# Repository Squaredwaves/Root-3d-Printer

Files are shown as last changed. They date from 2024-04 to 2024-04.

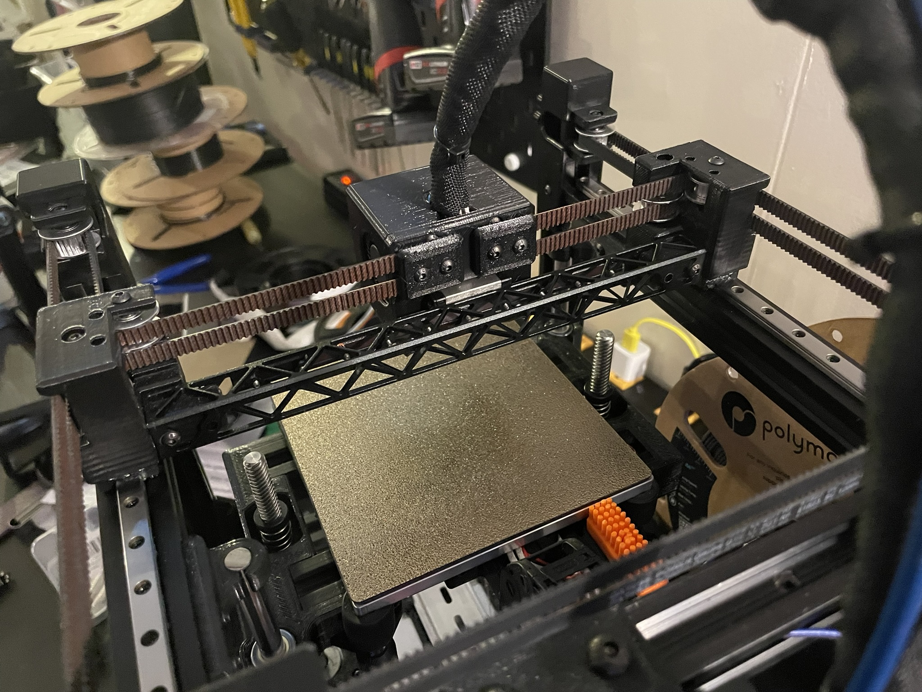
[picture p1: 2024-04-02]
Pics/Print head rear.jpeg

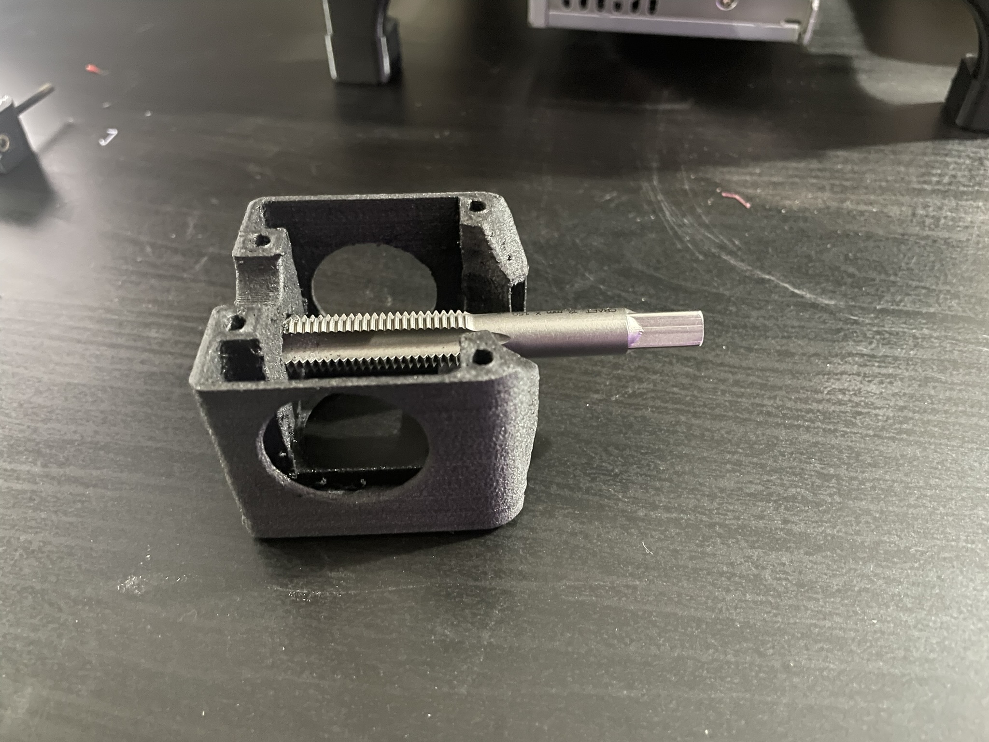
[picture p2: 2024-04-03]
Hot end assembly/IMG_1050.JPEG

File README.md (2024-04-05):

# Root-3d-Printer
Pics, files, and instructions for Root 3d Printer

Printables Link: https://www.printables.com/model/829074/edit

Instructions to come...



************Hot end assembly****************


Clean up any stringing or blobs as best as you can. This was some junk tier cf-petg


Run an m12x1.5 tap through threaded portion to chase threads and remove excess material




Press in m3 heat sets



Install heat break fan. Top first then bottom should clip in with a little pressure in the corners. Align wire so it doesn't get in the way


Prepare parts cooling fans by cliping the little plastic retainer on the fan and pulling the wire (gently) back



I will usually install the right one first but it probobly doesnt matter. They are a tight fit and may not come back out in one piece so make sure its how you want it.


Install Revo Micro hear break. I find a 10mm m4 bolt through the bottom helps a lot


Prep heater by CAREFULLY bending strain relief to a 90ish degree angle


Attach to heat break


Press 4 heat sets into back plate and attach to x axis linear rail
The completed hot end  bolts in from the back with m3 bolts

can see the top two bolts under belt retention

***************MOTOR MOUNTS ASSEMBLY********************




Press heat sets into shown location 


Thread 2 long m3 bolts from the bottomthrough the heatsets


Prep attachment bolts and hammer head nuts


Install in back corner of frame


Install motor with toothed pulley. I used a 2mm allen wrench between the motor body and pulley for spacing



Start installing pulleys. For left mount it will be 2 smooth on the inside and one smooth on the bottom one on the top on the outside(the picture is incorect on toothed pulley location) 2 or 3 3x5 .5mm shims go between the pulleys. Amazon link - https://www.amazon.com/gp/product/B08ZYLHGC9/ref=ppx_yo_dt_b_search_asin_title?ie=UTF8&th=1


Install top hat. Bolts should just poke through the top. 2 3mm bolts on either side hold to main body.


I don't know if its needed but I snugged acouple nuts on top

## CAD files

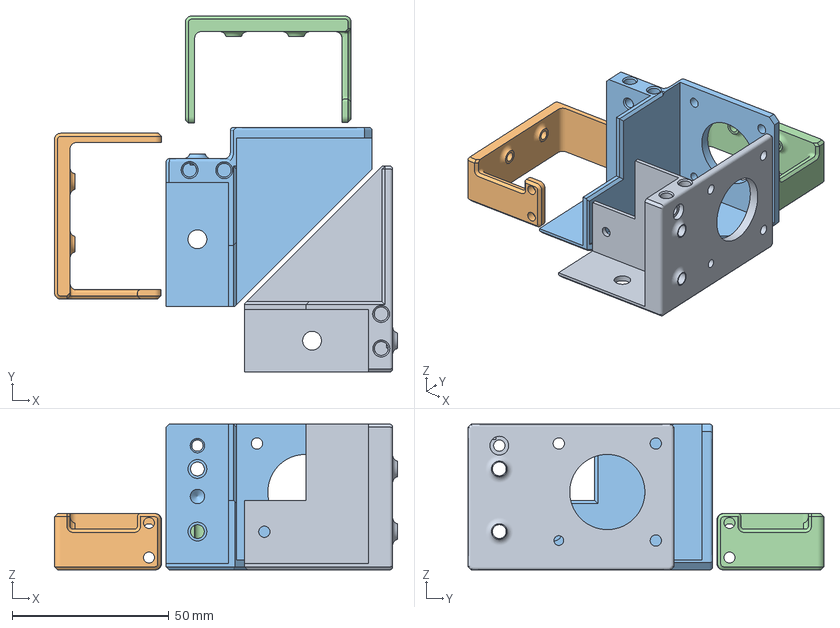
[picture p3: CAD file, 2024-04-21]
ROOT/REAR_CORNERS_MOTOR_MOUNTS.3mf
109.6 x 113.7 x 46.6 mm

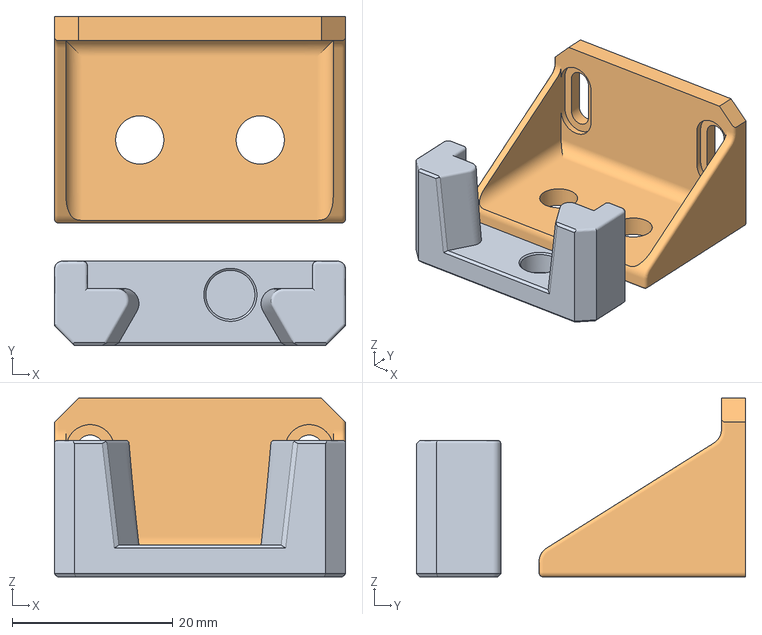
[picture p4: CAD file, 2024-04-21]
ROOT/KLICKYPCB_FRAMEMOUNT.3mf
36.3 x 41.0 x 22.3 mm

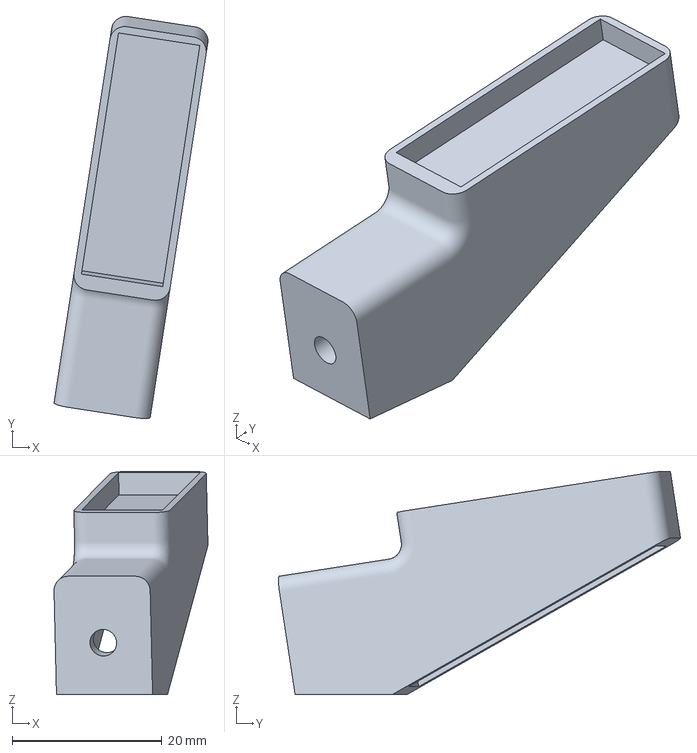
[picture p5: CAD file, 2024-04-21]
ROOT/NOZZLE_BRUSH.3mf
20.6 x 53.7 x 29.8 mm

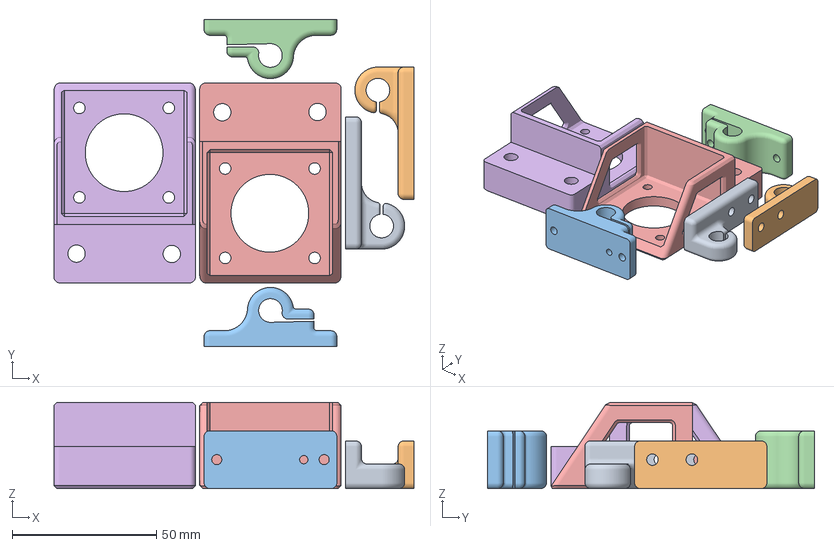
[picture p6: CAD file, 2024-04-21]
ROOT/Z_MOTION_MOTORS.3mf
124.7 x 113.4 x 29.8 mm
bed motor mounts.3mf
bed motor mounts.3mf(1)
bed motor mounts.3mf(2)
bed motor mounts.3mf(3)
bed motor mounts.3mf(4)
bed motor mounts.3mf(5)

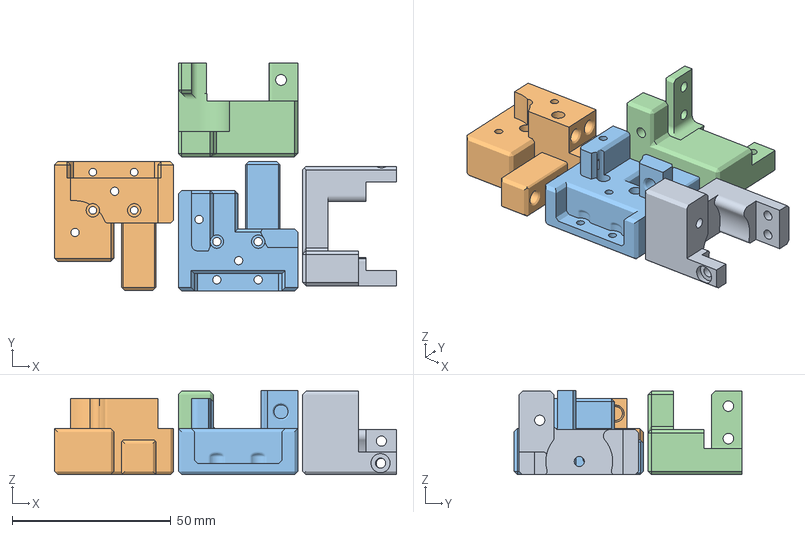
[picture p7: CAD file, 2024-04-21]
ROOT/XY.3mf
107.5 x 71.6 x 26.4 mm

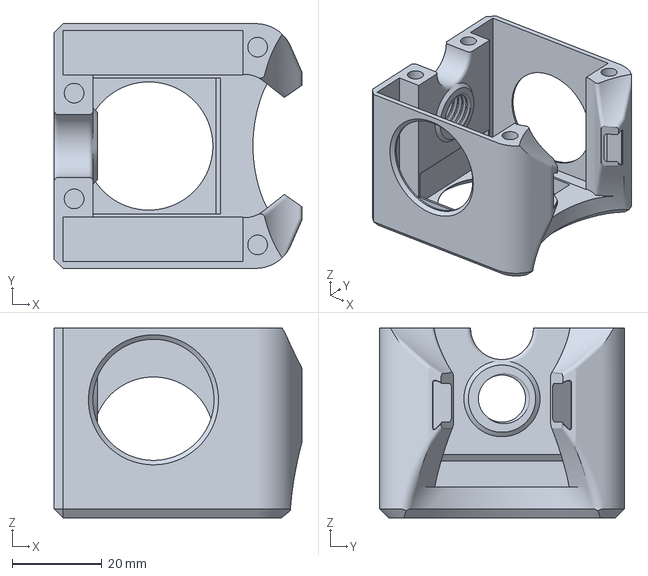
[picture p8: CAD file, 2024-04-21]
ROOT/FAN_SHROUD.3mf
55.3 x 54.6 x 42.3 mm

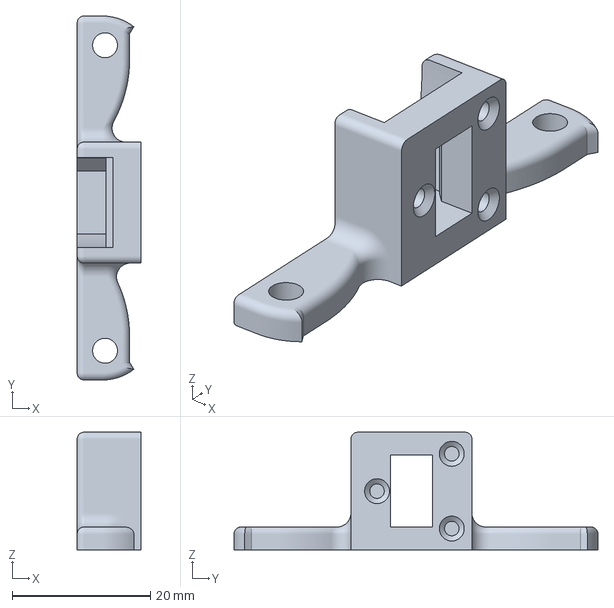
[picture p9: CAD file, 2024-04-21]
ROOT/Klicky_PCb_printmount.3mf
9.20 x 52.6 x 17.0 mm

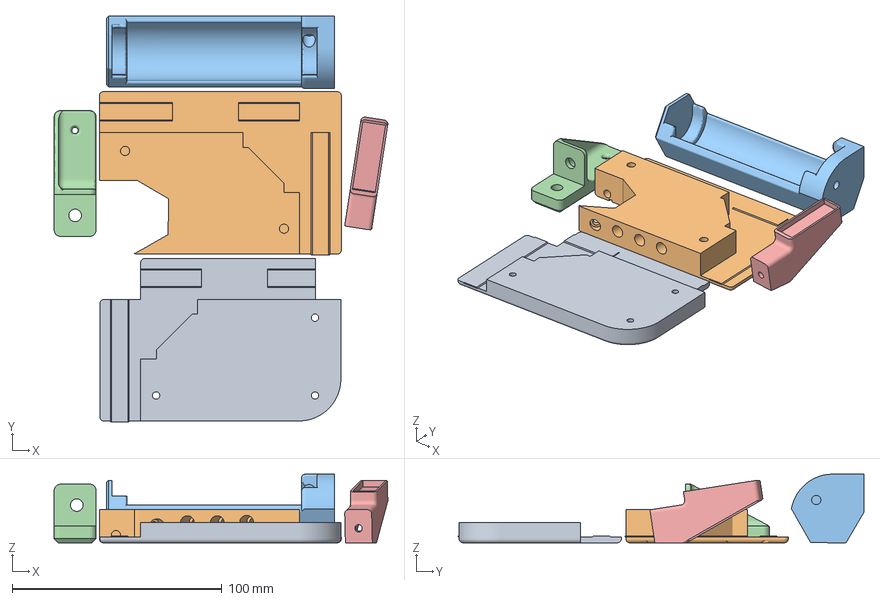
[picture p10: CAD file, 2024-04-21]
ROOT/FILAMENT_MANAGEMENT.3mf
159.1 x 193.6 x 32.8 mm
FILAMENT_MANAGEMENT.3mf(1)
FILAMENT_MANAGEMENT.3mf(2)
FILAMENT_MANAGEMENT.3mf(3)
FILAMENT_MANAGEMENT.3mf(4)
FILAMENT_MANAGEMENT.3mf(5)

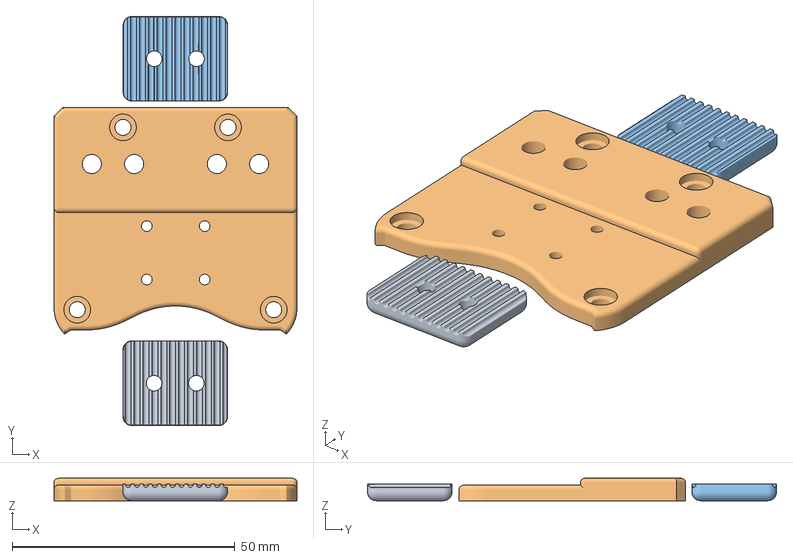
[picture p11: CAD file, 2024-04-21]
ROOT/PRINT_HEAD_TO_RAIL.3mf
54.6 x 91.9 x 5.06 mm
PRINT_HEAD.3mf
PRINT_HEAD.3mf(1)
PRINT_HEAD.3mf(2)

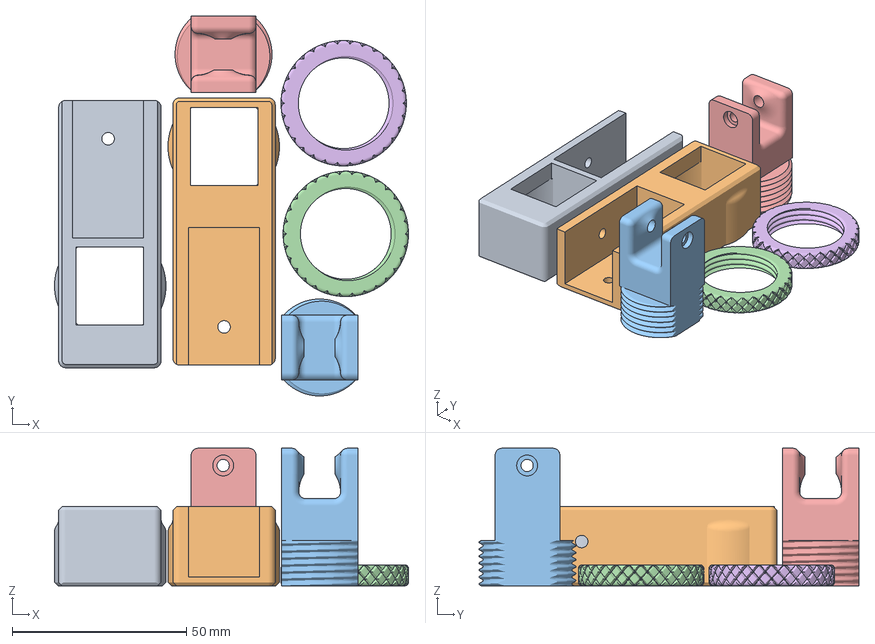
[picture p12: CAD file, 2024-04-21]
ROOT/FRONT_CORNERS_TENSIONERS.3mf
101.6 x 109.1 x 39.5 mm

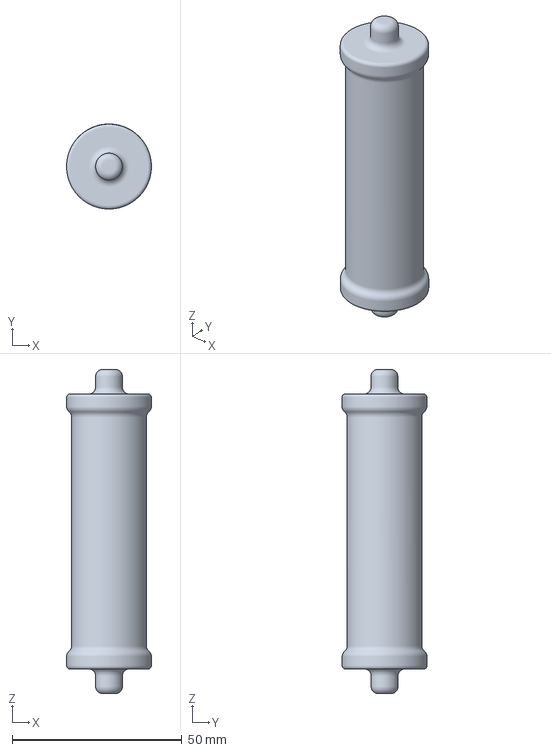
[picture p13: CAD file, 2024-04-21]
ROOT/FILAMENT_SPINDLE.3mf
25.0 x 25.0 x 95.4 mm

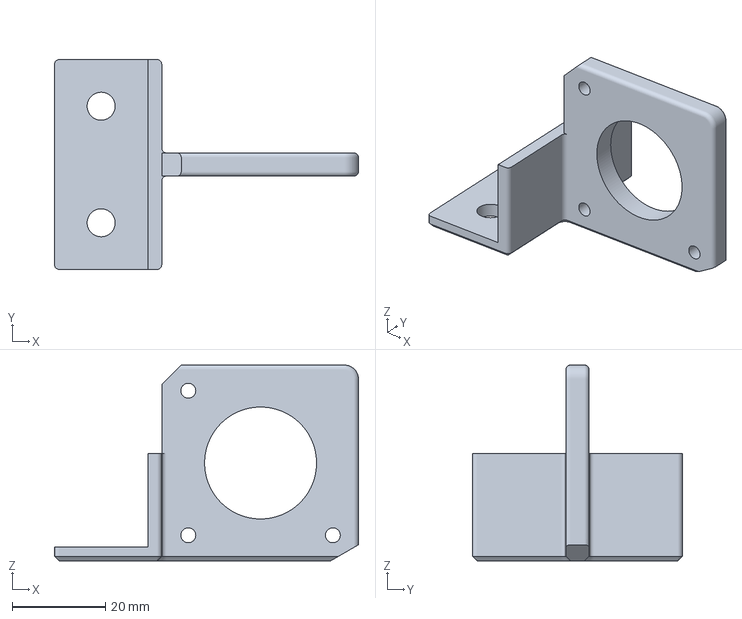
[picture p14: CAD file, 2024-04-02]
ROOT/EXTRUDER_BRACKET.3mf
65.2 x 45.0 x 42.0 mm

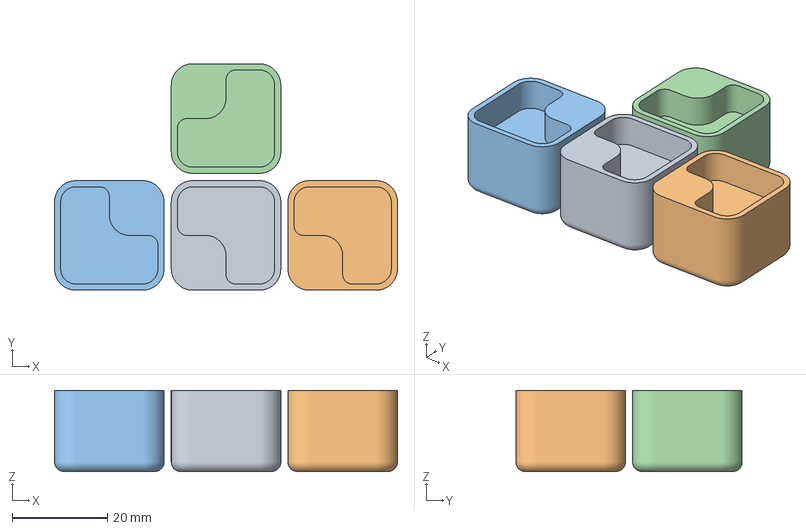
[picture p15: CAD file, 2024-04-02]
ROOT/ANTI_VIBRATION.3mf
72.0 x 47.5 x 17.0 mm
feet.3mf(6)
feet.3mf(4)
feet.3mf(2)
feet.3mf

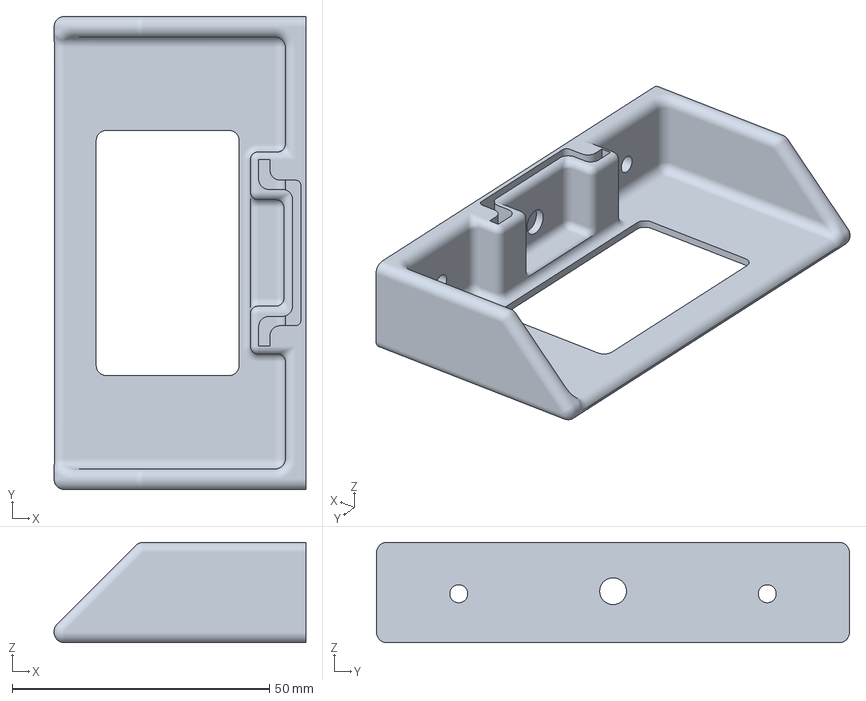
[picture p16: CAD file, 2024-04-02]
ROOT/PLUG_BRACKET_DIN_CAP.3mf
49.0 x 92.0 x 19.5 mm

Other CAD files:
ROOT/MGN7 BACKER.3mf
ROOT/CHAIN_MOUNTS.3mf
ROOT/BED_SUPPORT.3mf

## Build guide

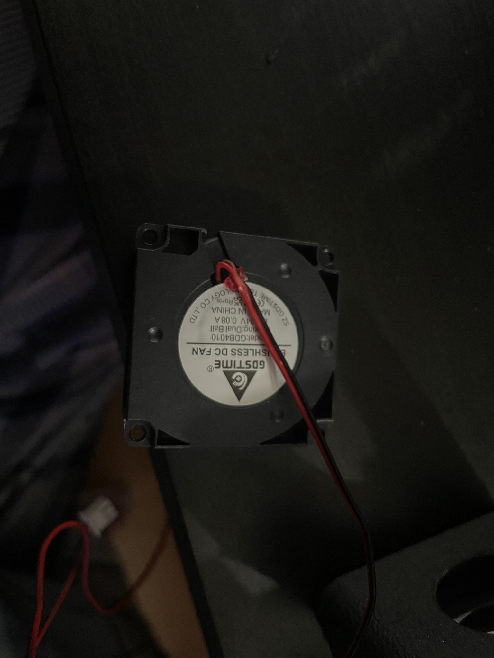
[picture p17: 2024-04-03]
Hot end assembly/IMG_1057.JPEG

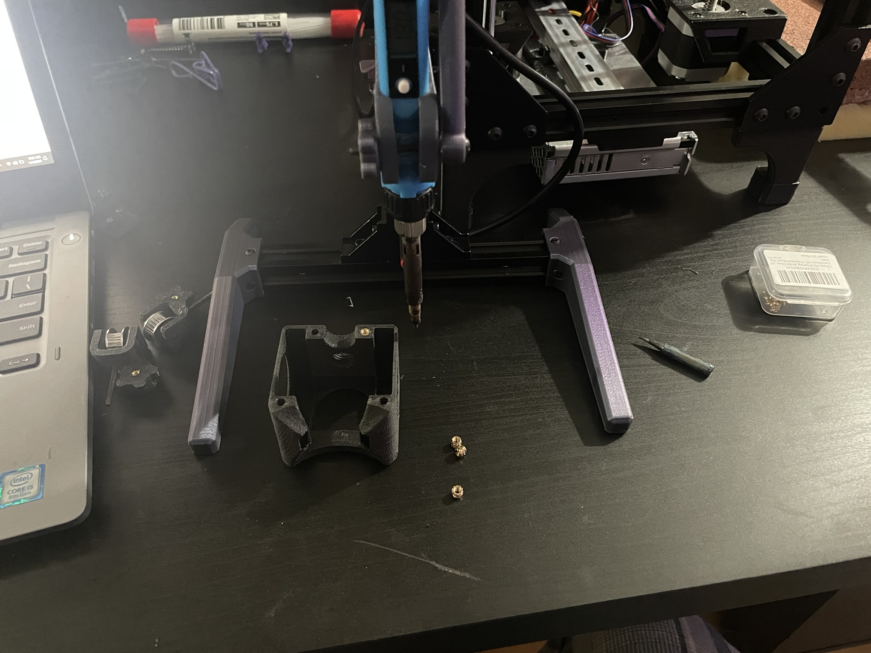
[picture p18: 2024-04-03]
Hot end assembly/IMG_1051.JPEG

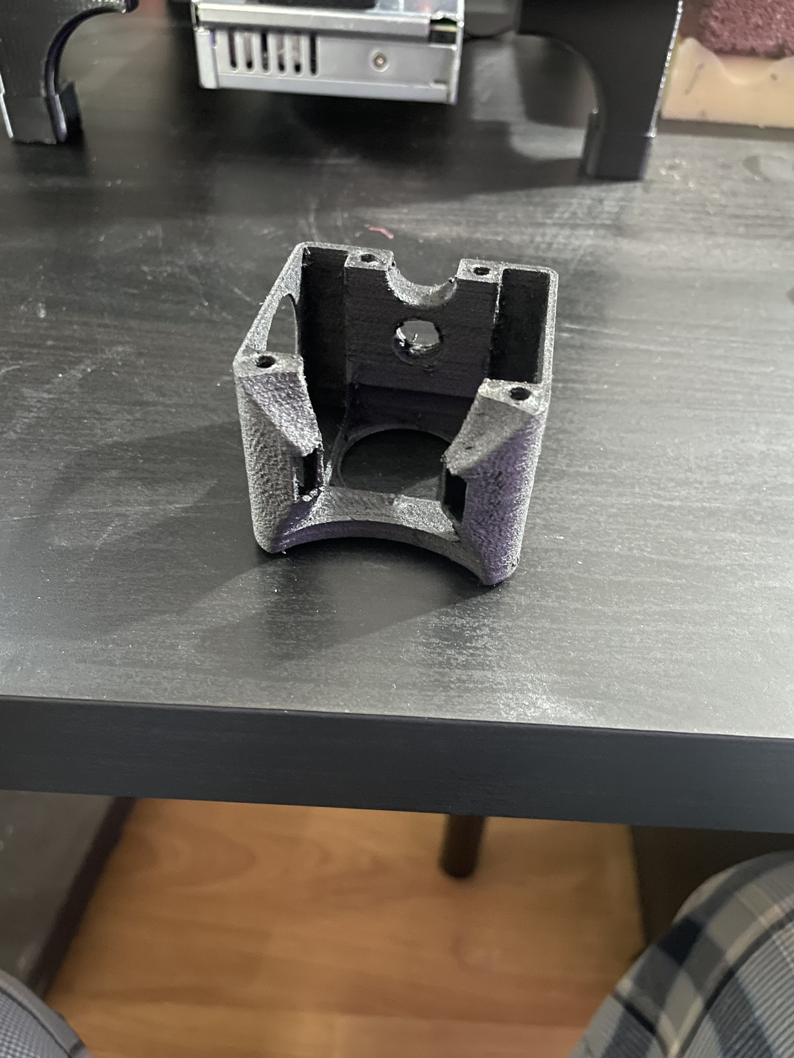
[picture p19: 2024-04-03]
Hot end assembly/IMG_1048.JPEG

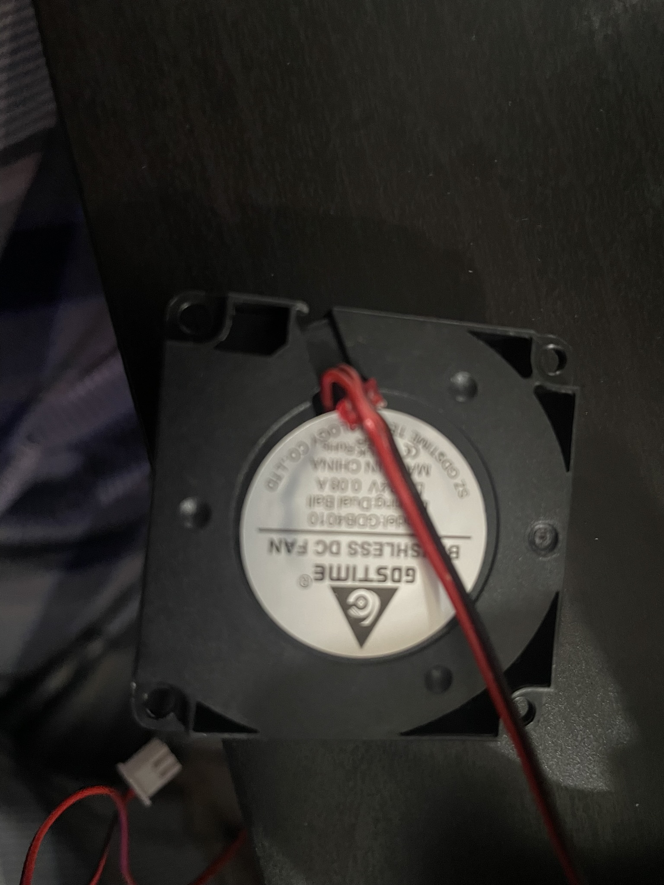
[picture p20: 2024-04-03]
Hot end assembly/IMG_1056.JPEG

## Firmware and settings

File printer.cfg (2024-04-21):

# This file contains common pin mappings for the BIGTREETECH SKR mini
# E3 v3.0. To use this config, the firmware should be compiled for the
# STM32G0B1 with a "8KiB bootloader" and USB communication/USART.

# The "make flash" command does not work on the SKR mini E3. Instead,
# after running "make", copy the generated "out/klipper.bin" file to a
# file named "firmware.bin" on an SD card and then restart the SKR
# mini E3 with that SD card.

# See docs/Config_Reference.md for a description of parameters.

[include klicky-probe.cfg]
[include KAMP_Settings.cfg]
[include mainsail.cfg]
[include K-ShakeTune/*.cfg]
[include macros.cfg]

[gcode_arcs]
resolution: 1.0
#   An arc will be split into segments. Each segment's length will
#   equal the resolution in mm set above. Lower values will produce a
#   finer arc, but also more work for your machine. Arcs smaller than
#   the configured value will become straight lines. The default is
#   1mm.

[exclude_object]

[stepper_x]
step_pin: PB13
dir_pin: !PB12
enable_pin: !PB14
microsteps: 64
rotation_distance: 20
endstop_pin: tmc2209_stepper_x:virtual_endstop
#endstop_pin: ^PC0
position_endstop: -1
position_min: -1
position_max: 120
homing_speed: 20
homing_retract_dist: 0

[tmc2209 stepper_x]
uart_pin: PC11
tx_pin: PC10
uart_address: 0
run_current: 1
#hold_current: 0.7
stealthchop_threshold: 0
diag_pin: ^PC0    # Set to MCU pin connected to TMC DIAG pin
driver_SGTHRS: 103 # 255 is most sensitive value, 0 is least sensitive
interpolate: false

[stepper_y]
step_pin: PB10
dir_pin: !PB2
enable_pin: !PB11
microsteps:64
rotation_distance: 20
#endstop_pin: ^PC1
endstop_pin: tmc2209_stepper_y:virtual_endstop
position_endstop: 139
position_min:-5
position_max: 139
homing_speed: 20
homing_retract_dist: 0

[tmc2209 stepper_y]
uart_pin: PC11
tx_pin: PC10
uart_address: 2
run_current: 1
#hold_current: 0.7
stealthchop_threshold: 0
diag_pin: PC1    # Set to MCU pin connected to TMC DIAG pin
driver_SGTHRS: 108 # 255 is most sensitive value, 0 is least sensitive
interpolate: false

[stepper_z]
step_pin: PB0
dir_pin: !PC5
enable_pin: !PB1
microsteps: 64
rotation_distance: 8
#endstop_pin: PC14
#position_endstop: 11.02
endstop_pin: probe:z_virtual_endstop
position_max: 125
position_min: -2
homing_speed: 20

[tmc2209 stepper_z]
uart_pin: PC11
tx_pin: PC10
uart_address: 1
run_current: .7
#hold_current: 0.500
stealthchop_threshold: 0
#diag_pin: ^PC2    # Set to MCU pin connected to TMC DIAG pin
#driver_SGTHRS:  45 # 255 is most sensitive value, 0 is least sensitive
interpolate: false

[extruder]
step_pin: PB3
dir_pin: PB4
enable_pin: !PD1
microsteps: 64
rotation_distance:   3.9403938
nozzle_diameter: 0.4
filament_diameter: 1.750
heater_pin: PC8
sensor_type: ATC Semitec 104NT-4-R025H42G
sensor_pin: PA0
#control: pid
#pid_Kp: 21.527
#pid_Ki: 1.063
#pid_Kd: 108.982
min_temp: 0
max_temp: 300
max_extrude_only_distance: 500
max_extrude_cross_section: 5
#max_extrude_only_accel: 4500
pressure_advance = .23

[tmc2209 extruder]
uart_pin: PC11
tx_pin: PC10
uart_address: 3
run_current: 1
#hold_current: 0.500
stealthchop_threshold: 0
interpolate: false
    
[bed_screws]
screw1: 5, 115
screw2: 115, 115
screw3: 60, 5

[heater_bed]
heater_pin: PC9
sensor_type: ATC Semitec 104GT-2
sensor_pin: PC4
#control: pid
#pid_Kp: 54.027
#pid_Ki: 0.770
#pid_Kd: 948.182
min_temp: 0
max_temp: 130

[heater_fan Heat_Break_fan]
pin: PC7
max_power: 1.0
heater_temp: 50.0
shutdown_speed: 1.0

[fan]
# FAN0
pin: PC6
max_power: 1.0
kick_start_time: 0.5                                                # Depending on your fan, you may need to increase this value if your fan will not start
off_below: 0.13
cycle_time: 0.010

[controller_fan controller_fan]
# FAN2
  pin: PB15
max_power: .6
kick_start_time: 0.5                                                # Depending on your fan, you may need to increase this value if your fan will not start
off_below: 0.13
cycle_time: 0.1

[mcu]
serial: /dev/serial/by-id/usb-Klipper_stm32g0b1xx_3B00500011504B5735313920-if00

#serial: /dev/ttyS0
#restart_method: command

[mcu host]
serial: /tmp/klipper_host_mcu

[adxl345]
cs_pin: host:gpio67
spi_bus: spidev0.0
axes_map:  x,-y,-z

[resonance_tester]
accel_chip: adxl345
#accel_per_hz: 100
probe_points: 60, 60, 110  # an example

[input_shaper]
shaper_freq_x: 106.2
shaper_type_x: mzv
shaper_freq_y: 119
shaper_type_y: mzv
damping_ratio_x: .083 # damping ratio for the X axis
damping_ratio_y: .087 # damping ratio for the Y axis

[temperature_sensor mcu_temp]
sensor_type: temperature_mcu
min_temp: 0
max_temp: 100

[temperature_fan btt_pi]
pin: host:gpio211
kick_start_time: 0.9
#shutdown_speed: 0
off_below: 0.3
max_power: 1.0
#fan_speed: 0.6
sensor_type: temperature_host
control: pid
min_temp: 0
max_temp: 85
#max_delta: 5.0
pid_kp: 1.0
pid_ki: 0.5
pid_kd: 2.0
min_speed: 0.0
max_speed: .6
target_temp: 38

[printer]
kinematics: corexy
max_velocity: 300
max_accel: 20000
max_z_velocity: 20
max_z_accel: 100
square_corner_velocity: 30




###########################################################
                           #Pins
[board_pins]
aliases:
    # EXP1 header
    EXP1_1=PB5,  EXP1_3=PA9,   EXP1_5=PA10, EXP1_7=PB8, EXP1_9=<GND>,
    EXP1_2=PA15, EXP1_4=<RST>, EXP1_6=PB9,  EXP1_8=PD6, EXP1_10=<5V>
    
#aliases:

# EXP1 header

#EXP1_1=PB5, EXP1_3=PA9, EXP1_5=PA10, EXP1_7=PB8, EXP1_9=<GND>,

#EXP1_2=PA15, EXP1_4=RST, EXP1_6=PB4, EXP1_8=PC0, EXP1_10=<5V>

################################################################

# BigTreeTech mini12864 v1mode

################################################################



######################################################################
#  BigTreeTech TFT TouchScreen emulated 12864 mode
######################################################################

#[display]
#lcd_type: emulated_st7920
#spi_software_miso_pin: PD8 # status led, Virtual MISO
#spi_software_mosi_pin: PD6
#spi_software_sclk_pin: PB9
#en_pin: PB8
#encoder_pins: ^PA10, ^PA9
#click_pin: ^!PA15

#[output_pin beeper]
#pin: PB5

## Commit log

2024-04-02 .cfg for SKR E3 V3
    set for sensor less homing and auto config. will have to put in your own motor info as well as host info. kinda sloppy
2024-04-02 .cfg for using SKR mini E3 V3 and BTT PI.
    [printer.cfg]
2024-04-02 Update printer.cfg
    Rearranged so it makes a little more sense and deleted shake-tune and auto-tune
    [printer.cfg]
2024-04-02 .3mfs for Root and master .step
    [ANTI_VIBRATION.3mf, BED_SUPPORT.3mf, CHAIN_MOUNTS.3mf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]
2024-04-02 Rename IMG_1045.jpeg to Z motor and PSU close up.jpeg
    named
2024-04-02 Rename IMG_1047.jpeg to Print head rear.jpeg
    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
2024-04-03 photos of hot end/ fan shroud assembly
2024-04-05 Update README.md
    motor mount instructions
2024-04-21 Delete ROOT directory
    DELETE FOLDER FOR NEW UPDATES
    [ANTI_VIBRATION.3mf, BED_SUPPORT.3mf, CHAIN_MOUNTS.3mf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]
2024-04-21 Add files via upload
    UPDATED MODELS
    [ANTI_VIBRATION.3mf, BED_SUPPORT.3mf, CHAIN_MOUNTS.3mf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]
2024-04-21 DELETED SOME STUFF
    [FILAMENT_MANAGEMENT.3mf, FILAMENT_SPINDLE.3mf, FRONT_CORNERS_TENSIONERS.3mf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]
